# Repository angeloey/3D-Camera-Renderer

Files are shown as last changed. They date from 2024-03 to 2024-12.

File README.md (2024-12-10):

//Angelo Maoudis README // 14074479 

# An Infrared 3D Camera & Graphics Renderer
Built from scratch as part of my Embedded Systems Programming Module

An embedded system to scan an object, then render the resulting scan in 3D to be inspected & interacted with by the user.

## 1 - Embedded System Proposal

Description: A 3D Scanner.
A device which scans a scene along the X and Y axis, while recording Z axis data about the scene. A 2D representation of the scene, alongside a 3D render is generated from the recoded data, which the user can interact with to inspect the object/scene post scan. Colour is used to represent depth in the 2d Image.

Basic operation:
The device uses a stepper motor and a servo to take range measurements in increments of 1 degrees, in a 90x90 degree FOV.\
The range measurements are made using an IR Sensor, the maximum range of which can be configured using an potentiometer.\
During and after completion of the scan, the data recorded is used to represent the scanned scene on the LCD Screen. The user can interact with a 3D render of the scanned scene via the touchscreen, or by selecting an option to automatically rotate the render via the rotary encoder menu.\
Uart Commands can also be used to start a scan remotely.

The system also contains customization options such a colour slider, and fov adjustment, which are modified in their corresponding menu via the touchscreen interface.

Verification of Successful Operation:
The fundamental operation of the system can be considered successful if a scene/object can be scanned by the device, producing a render which can be interacted with by user. I.e. can be rotate around all 3 Axis at will. A wide array of diferent technologies and peripherals will be used by the system to achieve this, and will work together without error or conflict.

## 2 - Hardware Design

Component List:

STM32f74NG-DISCO

Inputs:
 - Uart via Serial Port - STM32F74NG-DISCO
 - Potentiometer - NHP22
 - Rotary Encoder - EC11
 - IR Range Sensor - GP2Y0A21YK
 - Touchscreen - STM32F74NG-DISCO

Outputs:
 - Uart via Serial Port - STM32F74NG-DISCO
 - LCD Screen - STM32F74NG-DISCO
 - Servo Motor - SG90
 - Stepper Motor - PJJ051ZA-P

STM32F74NG-DISCO Datasheet: https://www.farnell.com/datasheets/1944312.pdf \
IR Sensor Datasheet: https://www.sparkfun.com/datasheets/Components/GP2Y0A21YK.pdf \
Potentiometer Datasheet: https://p3america.com/content/pdf/nhp22.pdf \
Rotary Encoder Datasheet: https://www.farnell.com/datasheets/1837001.pdf \
Servo Datsheet: https://static.rapidonline.com/pdf/37-1330t.pdf \
Stepper Motor Datsheet: University Provided, cannot find information online, generic unipolar stepper operation. \
ULN2803 Darlington Array Datasheet: https://www.st.com/resource/en/datasheet/uln2801a.pdf

Connection Diagram: \
connection diagram

System Runs on MbedOS 6 \
MbedOS Docs: https://os.mbed.com/docs/mbed-os/v6.16/introduction/index.html 

To stay within the "spirit" of the Embedded Systems Programming module, the System opts for software control over hardware control, via the GPIO, ADC, & DAC pins built in to the STM32f746NG-DISCO, with the only exception being the use of a ULN2803 Darlington Array IC which is used as a *driver* for the stepper motor. Stepper motor *control* is achieved via software implementation however.

## 3 - Embedded Code Implementation and Architechture

### Structure Overview

The system uses a combination of hard and soft interrupts, polling, and multithreading. \
This was an intentional design choice in order to demonstrate/implement a wider range of techniques. \
Hardware interrupts are used to control the physical IO of the device, such as the rotary encoder & menu navigation. \
Software interrupts (Tickers) are used to progress through the scanning process, as well as to refresh the LCD display. \
The touchscreen interface is handled by its own dedicated thread, running in paralell to the main thread of the device. Semaphores are used to manage the individual threads, and to ensure a thread only uses system resources when necessary. \
A polling scheme is used to manage the UART interface.  \
A flag polling system is also used to manage routines triggered by interrupts without executing them inside the ISR, both to avoid unwanted mutex locks, 
and to adhere to best practices (i.e. no delays or lengthy functions inside the ISR). 

Functionality of peripheral devices is contained and managed by individual Objects & corresponding libraries. 

All source files are commented where apporopriate to provide a reasonable level of documentation, "Pseudo Diagrams" have been drawn using comments in files where a greater level of explanation was felt necessary, example below from My-Stepper-Lib:

pseudodiagrams

### Tasks Handled by Software

### Scene/Object Scanning:
__Description__: The scanning routine is responsible for triggering & reading peripheral devices such as the stepper motor, servo, IR sensor,
and potentiometer. And displaying the progress of the scan to the user.
        
__Real-time Constraints__: During scanning data is collected from these peipherals, and output output to the motors in realtime as the scan progresses.
A 2D representation of the scene, as well as a 3D render of the scanned object is updated in realtime to indicate scan progress to the user.
        
__Responsiveness__: The system only allocates resources to areas required by this routine as and when they are needed. These resources are managed by a series of flags set and unset by the Scanning routine as the scan progresses.

### Hardware Interface Interaction:
__Description__: A rotary encoder is used to cycle through a menu, which provides primary method of user interaction with the system.
        
__Real-time Constraints__: This is handled using hardware interrupts, and will take priority over all tasks so that the user can control the device               without hinderence, with the exception of the scanning routine. If the scanning routine is currently running, the vertices from the last successfull scan are loaded into the vertex buffer before executing any instructions, to avoid any unfinished scans being loaded by the renderer.
        
__Responsiveness__: As mentioned above, this is handled by hardware interrupts to provide immediate response to user interaction.

### Touch Interface:
__Description__: Detecting touch on the LCD in specific areas, and executing tasks accordingly. The touch interface consists of 9 touch buttons used to rotate a scanned object in 3D, as well as to alter the camera focal length of the renderer. Additionally a slider is also used to change the draw colour of the system.
        
__Real-time Constraints__: Handled by its own dedicated thread that runs alongside the main thread of the system in order to respond to user interaction in realtime. \ This was intentional in order to demonstrate a wider range of technologies. Semaphores are used to ensure that the touch interface thread only consumes system resources when touchscreen buttons are visible on the screen.
        
__Responsiveness__: Since it is handled by its own thread, responsiveness to touch inputs is immediate, and has support for multiple simultaneous touches

### Uart Interface:
__Description__: A barebones uart interface is used to trigger the scanning routine remotely, upon recieveing a newline (\n) character via the serial port, the device compares the characters stored in its character buffer to a list of known commands, and executes hte corresponding command accordingly. If none are found, it notfies the user that it does not recognise the recived command. This was included primarily to better satisfy the marking criteria and demonstrate the use of serial communication, but finds itself analagous to existing embedded systems where remote activation is a desired feature.

__Real-time Constraints__: Characters are added to a buffer as and when they are recieved by the device, not particularly time-critical and is polled once any set flags have been acknowledged.

__Responsiveness__: No noticeable delay by the user. Effectively immediate from a humans POV.

### 3D Rendering:
__Description__: The device is capable of representing the data recorded by the scanning routine in the form of a weak perspective projection. The files inside folder My-3D-Lib are heavily commented to explain how the 3D rendering of the system is achieved, below is an attempt to illustrate how the "Projected" pixel coordinates are calculated from the vertices recorded by the Scanning routine, for the X axis. This process is repeated for each coordinate recorded (90 x 90 = 8100).

3d_rendering

 Triangles (X, Adjacent, C) and (Xp, Focallength, C) are similar, \
 therefore: Xp / X  ==  FocalLength / Adjacent \ 
 thus Xp  ==  (Focallength * X) / Adjacent \
 Xp (xProjected) is the X coordinate of the pixel intersected when casting a ray from the camera to the object. \
 Repeat for Y. Process is analagous. \
 Repeating this process for all scanned coordinates results in a list of XY pixel coordinate which when drawn on the screen \
 form a weak perspective projection of the scanned Scene/Object. 

__Real-time Constraints__: During scanning, a 3D render of the scene is constructed in realtime as the system records more data. However this render does not need to rotate, and given that the scan operates at a frequency of 20Hz, and each pixel is calculated as its corresponding vertex is obtained in realtime, ample time is available to render the scene in realtime. \
Once the scan has completed, the object can be rendered, rotated, and inspected by the user. This involves significantly more computational overhead and the frame-rate of the system is limited by the speed at which the FPU can complete these calculations.

__Responsiveness__: When rotating and inspecting the render, the system becomes significantly less responsive, and "Double-Buffering", along with V-Sync was implemented in order to eliminate screen tearing/flickering, as the device cannot calculate and draw all of the projected vertices fast enough to be imperceptible without this.

### Source Code Authors
Files written by me: 
 - Everything in a folder labelled "My-X"
 - main.cpp
 - README.md
 - Unit tests inside folder TESTS (Made from boilerplate provided in mbed docs, link to boilerplate provided as comments inside each file).
 All files are labelled with Name and SID as top comments.

Third-Party Code: 
 - BSP_DISCO_F746NG.lib
 - Mbed-OS.lib

### Practical Embedded Considerations

The scan system was originally made using an ultrasonic sensor, and a library for this sensor sourced from mbed.org, however the output was noisy and I intend to write all libraries for components myself. To solve this issue replaced with IR range sensor (much less noisy output) and wrote library from scratch (My-IR-Lib).

In order to target the IR Range sensor at a specific point, a Mount was designed and 3D-Printed, the latest version of this model in STL format is included in the repository under folder: 3D Print Files

The image below shows from left to right, Versions 1, 2, 3, & 4, of the aforementioned mount:

3d_mounts

Rotating a perspective projection render in 3 dimensions is computationally expensive, and somewhat out of reach for a device such as the STM32F7 to do in any reasonable amount of time. However this system takes advantage of a "workaround". 
Provided you only rotate around one axis at a time, a perspective projection can be rotated using the 2D rotation matrix, which is much less computationally expensive.
To provide rotation around all 3 axis, this system rotates around one axis, saves the result to a buffer, and then rotates the resulting buffer around another axis sequentially. this workaround means that the system can appear to rotate a render around 3 axis simultaneously, albeit while taking 3 times as long to do so.

Functionality was written into the stepper library to enable microstepping, however the STM32f7 Board being used for this system only has 2 onboard ADC's and the implementation (the only way i could think of to do it in software) required 4 ADC's to operate. 
As the step size of the provided stepper motor is too large for the degree of accuracy desired, the system only rotates the stepper every 4 degrees instead of every 1 degree, and takes 4 measurements during its travel time to acquire the closest approximation I could get. 
I am unable to find any information on this specific stepper online, but measuring its step size by hand, it appears to have a step size of ~7.5 Degrees, so I am using half stepping to get this down to ~4, and using the aforementioned method to compensate for it.

## 4 - Evaluation 
### Implementation Successfulness
The system achieves the criteria outlined in the proposal, it is capable of scanning scenes or objects and generating a 3D render which the user can freely rotate along all three axis. It utilises a wide range of technologies and peripherals, which operate without conflict. 
The system can be considered a sucessful prototype.

Upon reflection, some shortcomings of the device or things I would add given more time include:
- Ability to export renders to another device (maybe as .STL or similar).
- The stepper motor used for the project works fine as a proof of concept/prototype however in a future iteration i would substitute it for a stepper with a smaller minimum step angle, or use a MCU with multiple DAC's as to utilize microstepping
- Create an enclosure or housing for the device (Maybe a battery powered handheld iteration)
- Create a PCB implementation instead of relying on a breadboard
- Add greater functionality to the uart interface. a HC-05 module could be used along side a terminal app, to control the device from a phone

### Group Members:
Angelo Maoudis 14074479 \
Commits as: maoudisa(University Github) & angeloey (Home Github). 

## Link to Video Demonstration:
https://youtu.be/fXoxNYmKON4

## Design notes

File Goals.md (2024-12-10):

### Goals & Pre-Project Discussion:
Goals for the Assignment. \
Namely, the objectives defined in the marking criteria, and how i intend to achieve each one.

#### Grade:
100%.
Satisfy all marking criteria to a maximum

#### Complexity (Technologies):
the goal of the project will be to develop the aforementioned embedded system using a range of technologies as to satisfy the assignment criteria.\
The system will purposely include a range of technologies, even in scenarios where it would traditionally make sense to use multiple instances of a
single technology, for example: instead of using two stepper motors (one for x movement and one for y movement), this project will make use of a
stepper motor for x movement and a servo motor for y movement.\
or by using a rotary encoder and a potentiometer, where two potentiometers would suffice.\
While this may not be the most practical approach, it affords me the opportunity to write a library for, and implement the use of more technologies which will better aid the achievement of the following excerpt from the marking criteria:

*"a wide range of complex\
input and output devices some of\
which we may not have used in\
the tutorial material, all working\
as expected."*

#### Version Control (Regular Commits and a Clear Workflow):
Another goal of the project is to provide a meaningful and well commented/documented update to the repository at regular intervals. \
(I will aim for daily commits, however: life waits for no man.) \
Any periods without a commit will be compensated for in magnitude or quantity once updates resume. \
There are 27 days between the start of this project on March 6th, and the due date April 2nd, therefore I will ensure there are at MINIMUM, 27 commits of
substanstial size, quality, or progress before April 2nd. \
Each commit will aim to demonstrate a clear direction and progress route through the projects development, i.e. evidence i havent just copied a load of
stuff i dont understand from stackoverflow.

I consider a meaningful update to be along the lines of, but not limited to, the following :

 - Functional progress in, or the completion of, a library for a component (.h and .cpp files in folder designated: "My-X-Lib"). 
 - Well commented, significant progress on the functionality of the project. 
 - Significant progress in, or beginning of, the Implementation of a new technology (a functional addition to debug screen for example.).
 - "Housekeeping": formatting, commenting, & encapsulating code to better reflect OOP practices etc.
 - Checkoints, functional milestones, or working implementation of a feature, such as a demo (i.e. "50Hz Rotating Cube Demo" on March 18th).

TL;DR:
Regular updates of some significance, with an accurate commit message.\
No "added some code" commits.\
Clear workflow and direction should be visibile throughout commit history (once target embedded system has been decided).\

this is with the intention of achieving the following assignment criteria excerpt:

*"Evidence of regular daily\
commits over a longer time\
frame. Demonstrates clear\
incremental progress with logical\
commit messages for features etc."*

#### Code Quality:
Write practical code and follow best practices throughout all aspects of the assignment, including but not limited to things such as:

 - dont use delays in an interrupt, dont use GOTO: etc.
 - dont name variables things like: "foo", "bar", and "var1", code should be "self documenting" and readable.
 - use MEANINGFUL comments as a form as documentation, no functions without comments, but also dont have a useless comment on every single line.
 - need to call the same bit of code many many times? PUT IT IN A FUNCTION/CLASS/LIBRARY.
 - camelCase is king.
 - dont use uint32_t where uint8_t would suffice. not exclusive to integers. *(Exception: Chris said it's ok to "throw floats at it")*

(I will consider myself exempt from these restrictions during development/debugging, however final code should follow all without exception). \
the following assignment criteria is self explanitory, I will attempt to be a good code monkey:

*Outstanding tidy code. Good\
practices being used e.g.\
encapsulation, meaningful\
identifiers and an attempt at\
documentation. Code contains\
no linting errors or warnings."*

Additional overlap from the following excerpt:

*"Use of custom classes, objects,\
and OOP concepts."*

### Naming Convention adhered to:
- Variables: camelCase
- User-Defined/Custom Types: PascalCase
- Constants: CAPS_SEPARATED_BY_UNDERSCORES
- Private Member Variables: /_underscorePrefixedCamelCase
- Descriptive Self-Documenting identifiers are mandatory. 

#### Complexity & Architechture (Embedded Code)

the following criteria is self explanitory, dont have the entire thing in a while loop:

*"The embedded architecture used\
likely makes use of a\
combination of hard and soft\
interrupts with polling or perhaps,\
RTOS, multi-threading, event\
loops, etc."*

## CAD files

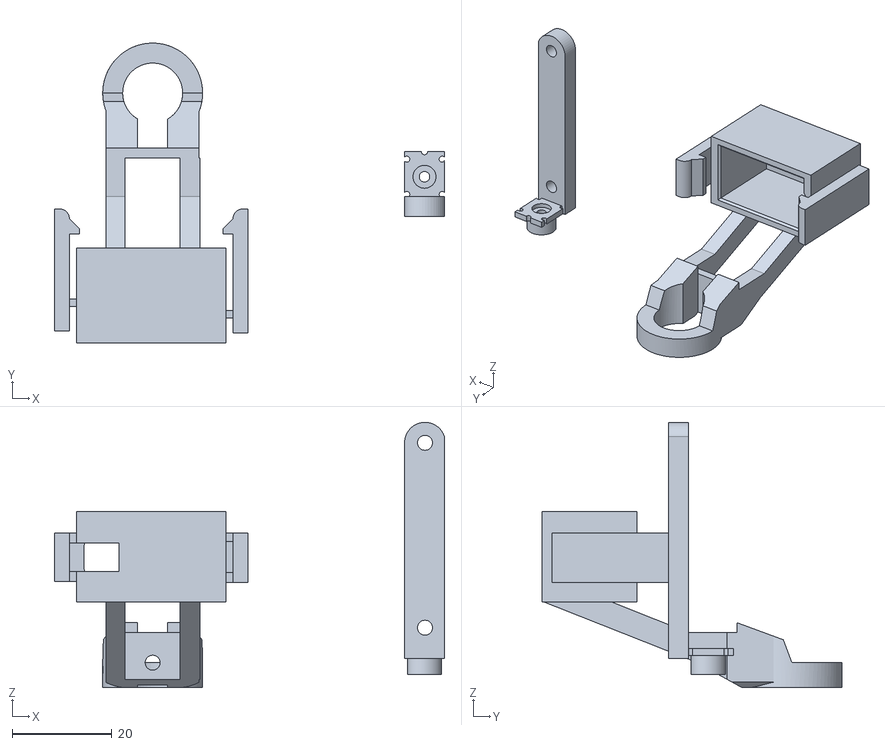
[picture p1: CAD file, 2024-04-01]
3D Print Files/Angelo_IR_Mount_V4.stl
78.1 x 60.0 x 53.1

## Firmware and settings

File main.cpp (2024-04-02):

// Angelo Maoudis 14074479
#include "mbed.h"
#include "rtos.h"
#include "stm32746g_discovery_lcd.h"
#include "stm32746g_discovery_ts.h"
#include "math.h"
// My Libs
#include "irSense.h"
#include "myUtils.h"
#include "pot.h"
#include "myServo.h"
#include "myStepper.h"
#include "rotaryEncoder.h"
#include "my3d.h"
#include "myButtons.h"
#include "uartCommands.h"

    // Magic Numbers / Constants                 // Using constexpr over #define for evaluation at compile time. Considered better practice in modern c++
namespace constants{
        // Menu/Option Constants
    constexpr int8_t MAX_MENU_ENTRIES = 4 -1;
        // Offsets/Coordinates for drawing on LCD
    constexpr uint8_t OFFSET_3D_X = 240;         // Offsets for drawing 3D object centred on (0,0) which is at the top left of the LCD.
    constexpr uint8_t OFFSET_3D_Y = 127;
    constexpr uint8_t OFFSET_RADAR_X = 110;      // Position offsets for drawing radar view.
    constexpr uint8_t OFFSET_RADAR_Y = 202;
    constexpr uint16_t OFFSET_DEPTHMAP_X = 310;  // Position offsets for drawing depth map.
    constexpr uint8_t OFFSET_DEPTHMAP_Y = 202;
}

    // Function declarations
void incrementScan(void);
void drawRadarView(float distance, float angle);
void drawDepthMap(float irDistance, float scanAngle, uint8_t scanLayer, uint8_t maxRange);
void updatePeripherals(float currentIrDistance, float currentScanAngle, uint8_t currentScanLayer, float currentPotReading);
void rotaryButtonPressed(void);
void rotaryTurned(void);
void draw3dObject(void);
void rotatingCubeDemo(void);
void drawDebugCube(void);
void manualRotation(void);
void tsButtonThreadFunction(void);
void toggleLCDLayer(void);
void startScanUart(void);

    // Obtaining XYZ values via scan
bool scanningClockwise = false; // Scan direction: False = CCW(-X), True = CW(+X) 
int8_t desiredScanAngle = 0;   // Scan/Stepper angle (Horizontal/X Axis)
uint8_t depthMapLayer = 0;      // Y value/layer of depthmap, also used for Servo angle (Vertical/Y Axis)
uint8_t rangeCutoff = 100;      // Any distances sensed past this value, are capped to this value (Depth/Z Axis)

    // Flags, mostly for executing functions incompatible with ISR (mutex, too slow, etc.)
bool progressScanFlag = false;  // Scan object flag, progress through 3D scan when this flag is set.
bool draw3dObjectFlag = false;  // Draw 3D object when this flag is set.
bool spinRenderFlag = false;    // Rotate 3D object automatically when this flag is set.
bool rotateTouchFlag = false;   // Enable touch buttons flag.
bool loadTestCubeFlag = true;   // Until this flag is un-set, 3D renderer draws a tri-coloured cube.
bool drawDebugFlag = false;     // Draw Debug-Screen. Peripheral data, etc.

    // Menu navigation/control
int8_t menuCounter = 0;         // Used to store last/select a menu option via rotary Encoder.
uint8_t rotationAxis = 0;       // Axis of rotation for 3D objects. 0, 1, 2 == X, Y, Z.
uint16_t pixelIndex = 0;     // Current xyz index to write/read.

    // Misc.
uint32_t drawColour = LCD_COLOR_YELLOW; // This is modified by SliderDrawColour. Default setting is yellow.
uint8_t redArgb = 0xFF;                            
uint8_t greenArgb = 0xFF;                // ARGB values, used to cycle through ARGB spectrum via slider. Alpha is always 0xFF when these are used
uint8_t blueArgb = 0xFF;                 // Default is 0xFF (255) (white)
uint16_t lastX;                          // Coordinates of last drawn line for radar view, used to overwrite in black without clearing entire radar.
uint16_t lastY;                          // purely cosmetic.
int activeLCDLayer = 0;

    // Initialization, Peripheral Objects/Structs.
IrSense IR(A0);                                     // initialize IR sensor, reading from Pin A0
Pot RangePot(A1);                                   // initialize Potentiometer, reading from Pin A1
Servo Servo(D0, 90, 2, 1.5);                     // initialize Servo motor, on pin D0, with a 180 degree range between 1.5 and 2ms.
Stepper Stepper(D1, D2, D3, D4, 7.5);               // initialize Stepper motor, on pins D1, D2, D3, D4, with a step angle of 7.5
Rotary Encoder(D5, D6, D7, &rotaryButtonPressed, &rotaryTurned);    // initialize Rotary Encoder on D5,D6,D7, and pass functions to object
//MicroStepper Stepper(A5, A4, A3, A2, 7.5);        // Cant use microstepping as the board only has 2 DAC outs :(
Object3D Render3D(-200);  // initialize 3D Object
TS_StateTypeDef Touchstate;                         // Touchscreen-state Struct
UartInterface UartSerial(USBTX, USBRX, 115200, &startScanUart);

    // Initialization, Touchscreen Button Objects
Button ButtonIncreaseRotationX(420, 460, 52, 92, LCD_COLOR_RED, LCD_COLOR_YELLOW, 1, Touchstate);               // Rotate around z axis
Button ButtonDecreaseRotationX(420, 460, 180, 220, LCD_COLOR_RED, LCD_COLOR_YELLOW, 2, Touchstate);
Button ButtonDecreaseRotationY(140, 180, 225, 265, LCD_COLOR_GREEN, LCD_COLOR_YELLOW, 3, Touchstate);           // Rotate around y axis.
Button ButtonIncreaseRotationY(300, 340, 225, 265, LCD_COLOR_GREEN, LCD_COLOR_YELLOW, 4, Touchstate);
Button ButtonIncreaseRotationZ(20, 60, 52, 92, LCD_COLOR_BLUE, LCD_COLOR_YELLOW, 5, Touchstate);                // Rotate around z axis.
Button ButtonDecreaseRotationZ(20, 60, 180, 220, LCD_COLOR_BLUE, LCD_COLOR_YELLOW, 6, Touchstate);
Button ButtonResetRotation(350, 470, 230, 262, LCD_COLOR_MAGENTA, LCD_COLOR_CYAN, 0, Touchstate);               // Restore to saved vertices.
Button ButtonDecreaseFov(75, 130, 230, 262, LCD_COLOR_DARKCYAN, LCD_COLOR_WHITE, 0, Touchstate);                // fov-, Increases focal length.
Button ButtonIncreaseFov(10, 65, 230, 262, LCD_COLOR_DARKBLUE, LCD_COLOR_WHITE, 0, Touchstate);                 // fov+, Decreases focal length.
Slider SliderDrawColour(10, 65, 10, 42, LCD_COLOR_LIGHTMAGENTA, LCD_COLOR_WHITE, 0, Touchstate, true, 30, 450); // Change drawing colour via slider

    // Classes/Mbed Objects, Tickers/Interrupts/Etc.
Utilities Utils;            // Utilities class. Frequently used, non program-specific functions.
Ticker TickerNextStep;      // used to iterate through object scan
Ticker TickerUpdateScreen;  // Refresh screen with updated view from selected mode, normally 50Hz

    //Threads / RTOS / Mutex
Thread ThreadTSButtons;       // Dedicated thread for handling TS Button Presses
Mutex MutexTSButtons;         // Mutex lock for when reset button needs to load (8100*3) vertices.
Semaphore SemaphoreTSButtons(1, 1); // Semaphore, used to control execution of TS Button thread

//----------------------------Function definitons--------------------------------------------
    // Used to start scan via uart
void startScanUart(void){
    BSP_LCD_Clear(LCD_COLOR_BLACK);
    TickerUpdateScreen.detach();
    TickerNextStep.detach();
        // Attatch ticker to this flag. Increments scan progress
    TickerNextStep.attach(incrementScan, 20ms); // 50Hz
}

    // Select & Execute menu options when button is pressed // Triggered by interrupts in rotary lib
void rotaryButtonPressed(void){
    for(int i = 0; i < 2; i++){
        BSP_LCD_Clear(LCD_COLOR_BLACK);
        switch(menuCounter){
        case 0:
            TickerUpdateScreen.detach();
            TickerNextStep.detach();
                // Attatch ticker to this flag. Increments scan progress
            TickerNextStep.attach(incrementScan, 20ms); // 50Hz
            break;
        case 1:
            TickerUpdateScreen.detach();
            TickerNextStep.detach();
                // Attatch ticker to this flag. Redraws Object
            TickerUpdateScreen.attach(draw3dObject, 20ms); // 50Hz
            spinRenderFlag = true;
            break;
        case 2:
            TickerUpdateScreen.detach();
            TickerNextStep.detach();
                // Restore 3D object from save
            Render3D.restoreSave();
                // Draw buttons
            BSP_LCD_SetTextColor(LCD_COLOR_ORANGE);
            BSP_LCD_DrawRect(79, 49, 321, 156);
            ButtonIncreaseRotationX.drawButton(); ButtonDecreaseRotationX.drawButton();
            ButtonIncreaseRotationY.drawButton(); ButtonDecreaseRotationY.drawButton();
            ButtonIncreaseRotationZ.drawButton(); ButtonDecreaseRotationZ.drawButton();
            ButtonIncreaseFov.drawButton(); ButtonDecreaseFov.drawButton();
            ButtonResetRotation.drawButton();
            SliderDrawColour.drawButton();
            BSP_LCD_SetFont(&Font16);
            BSP_LCD_SetTextColor(LCD_COLOR_YELLOW);
            BSP_LCD_DisplayStringAt(80, 241, (uint8_t*)"fov-", LEFT_MODE);
            BSP_LCD_DisplayStringAt(15, 241, (uint8_t*)"fov+", LEFT_MODE);
            BSP_LCD_DisplayStringAt(365, 241, (uint8_t*)"reset", LEFT_MODE);
            BSP_LCD_SetFont(&Font12);
                // Attatch ticker to this flag. Rotates and draws based on ts input
            TickerUpdateScreen.attach(manualRotation, 1ms); // 50Hz
            break;
        case 3:
            drawDebugFlag = !drawDebugFlag;
            break;
        default:    // should never happen
            BSP_LCD_DisplayStringAt(0, LINE(1), (uint8_t *)"Something went wrong (rotaryButtonPressed)", CENTER_MODE);
            break;
        }
    }
}

    // Scroll through menu when Encoder is turned
void rotaryTurned(void){
    (Encoder.getClockwise() == true) ? menuCounter++ : menuCounter--;
    if(menuCounter > constants::MAX_MENU_ENTRIES){
        menuCounter = 0; 
    }else if(menuCounter < 0){
        menuCounter = constants::MAX_MENU_ENTRIES;
    }
    BSP_LCD_ClearStringLine(1);
    BSP_LCD_SetTextColor(LCD_COLOR_YELLOW);
    switch(menuCounter){
        case 0:
            BSP_LCD_DisplayStringAt(0, LINE(1), (uint8_t *)"Menu: Start Scan", CENTER_MODE);
            toggleLCDLayer();
            BSP_LCD_DisplayStringAt(0, LINE(1), (uint8_t *)"Menu: Start Scan", CENTER_MODE);
            break;
        case 1:
            BSP_LCD_DisplayStringAt(0, LINE(1), (uint8_t *)"Menu: Rotate Scanned Object", CENTER_MODE);
            toggleLCDLayer();
            BSP_LCD_DisplayStringAt(0, LINE(1), (uint8_t *)"Menu: Rotate Scanned Object", CENTER_MODE);
            break;
        case 2:
            BSP_LCD_DisplayStringAt(0, LINE(1), (uint8_t *)"Menu: Manual Object Rotation", CENTER_MODE);
            toggleLCDLayer();
            BSP_LCD_DisplayStringAt(0, LINE(1), (uint8_t *)"Menu: Manual Object Rotation", CENTER_MODE);
            break;
        case 3:
            BSP_LCD_DisplayStringAt(0, LINE(1), (uint8_t *)"Menu: Debug Mode", CENTER_MODE);
            toggleLCDLayer();
            BSP_LCD_DisplayStringAt(0, LINE(1), (uint8_t *)"Menu: Debug Mode", CENTER_MODE);
            break;
        default:    // should never happen
            BSP_LCD_DisplayStringAt(0, LINE(1), (uint8_t *)"Something went wrong (rotaryTurned)", CENTER_MODE);
            break;
    }
}

    // Draw radar representaion of current scan (X&Z progress along each Y layer)
void drawRadarView(float irDistance, float scanAngle){ 
    BSP_LCD_SetTextColor(LCD_COLOR_BLACK);
    BSP_LCD_DrawLine(constants::OFFSET_RADAR_X, constants::OFFSET_RADAR_Y, lastX + constants::OFFSET_RADAR_X, lastY + constants::OFFSET_RADAR_Y); // overwrite last drawn line in black
    uint16_t x = irDistance * cos(constants::PI_DOUBLE * 2 * (scanAngle + 225) / 360); 
    uint16_t y = irDistance * sin(constants::PI_DOUBLE * 2 * (scanAngle + 225) / 360); // find x,y coords of a point on a circle, of radius 'distance' at angle 'angle'
    BSP_LCD_SetTextColor(LCD_COLOR_WHITE);
    BSP_LCD_DrawLine(constants::OFFSET_RADAR_X, constants::OFFSET_RADAR_Y, x + constants::OFFSET_RADAR_X, y + constants::OFFSET_RADAR_Y); // draw a line from radar offset, to x,y + offset
    BSP_LCD_SetTextColor(LCD_COLOR_YELLOW);
    BSP_LCD_DrawCircle(x + constants::OFFSET_RADAR_X, y + constants::OFFSET_RADAR_Y, 1); // mark the end of the line with a yellow blob
    BSP_LCD_DrawLine(x + constants::OFFSET_RADAR_X, y + constants::OFFSET_RADAR_Y, lastX + constants::OFFSET_RADAR_X, lastY + constants::OFFSET_RADAR_Y); // connect the blobs
    lastX = x; // store last used x,y values
    lastY = y;
}

    // Draw 2D image with depth data. Closer distance = brighter pixel
void drawDepthMap(float irDistance, float scanAngle, uint8_t scanLayer, uint8_t maxRange){ 
    uint16_t drawX = (scanAngle) + constants::OFFSET_DEPTHMAP_X; //0-90deg from left = x coord 0 to 90 from offset //TODO: "normalise" the image so it isnt skewed 
    uint16_t drawY = constants::OFFSET_DEPTHMAP_Y - scanLayer;                                                     //(Z = cos(angle) * distance??? check maths before implementing)
    uint8_t redBrightness = Utils.valMap(irDistance, 0, maxRange, 0xFF, 0x00);
    BSP_LCD_DrawPixel(drawX, drawY, Utils.argbToHex(0xFF, redBrightness, 0x00, 0x00));
        // Draw bounding box
    BSP_LCD_SetTextColor(drawColour);
    BSP_LCD_DrawRect(constants::OFFSET_DEPTHMAP_X - 1, constants::OFFSET_DEPTHMAP_Y - 91, 91, 91);
}
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
int main(){
    
        // Setup LCD, Show startup message, Clear to black
    BSP_LCD_Init();
    BSP_LCD_SetXSize(480); BSP_LCD_SetYSize(272);
    BSP_LCD_LayerDefaultInit(LTDC_ACTIVE_LAYER, LCD_FB_START_ADDRESS);
    BSP_LCD_SelectLayer(LTDC_ACTIVE_LAYER);
    BSP_LCD_DisplayStringAt(0, LINE(5), (uint8_t *)"14074479 MAOUDISA", CENTER_MODE);
    HAL_Delay(1000);
    BSP_LCD_SetFont(&Font12);
    BSP_LCD_SetBackColor(LCD_COLOR_TRANSPARENT);
    BSP_LCD_SetTextColor(LCD_COLOR_WHITE);
    BSP_LCD_Clear(LCD_COLOR_BLACK);

        // Setup another LCD layer
    BSP_LCD_LayerDefaultInit(0, LCD_FB_START_ADDRESS +(272*480*4));
    BSP_LCD_SelectLayer(0);
    BSP_LCD_DisplayStringAt(0, LINE(5), (uint8_t *)"14074479 MAOUDISA", CENTER_MODE);
    HAL_Delay(1000);
    BSP_LCD_SetFont(&Font12);
    BSP_LCD_SetBackColor(LCD_COLOR_TRANSPARENT);
    BSP_LCD_SetTextColor(LCD_COLOR_WHITE);
    BSP_LCD_Clear(LCD_COLOR_BLACK);

        // Initialize touchscreen
    BSP_TS_Init(480, 272);

        // Attatch ticker to this flag. Using this demo as a splash screen
    BSP_LCD_SelectLayer(0); BSP_LCD_SetLayerVisible(0, ENABLE); BSP_LCD_SetLayerVisible(1, DISABLE);
    TickerUpdateScreen.attach(rotatingCubeDemo, 1ms); 

    // Do nothing here until a flag is set
    while(1) {

             // Wait for v-sync before drawing next frame. (Magic.)
        while (!(LTDC->CDSR & LTDC_CDSR_VSYNCS)) {}

            // Manual control over 3D render (Slow)
        if(rotateTouchFlag == true){
            toggleLCDLayer();
                // Relinquish control of Semaphore so TSButton thread can run
            SemaphoreTSButtons.release();
                // Attatch thread to monitor TS Buttons and rotate render accordingly, does nothing once thread is started.
            ThreadTSButtons.start(tsButtonThreadFunction);
                // Generate coordinates, Clear Object, Draw image. (Only clear immidiately before drawing to reduce strobing)
                // Buttons are not redrawn, But also not cleared. Faster. (Exception -> Sliders)
            Render3D.generateProjected();
            //SCB_CleanDCache();
            if(loadTestCubeFlag == true){
                drawDebugCube();
            }else{
                BSP_LCD_SetTextColor(LCD_COLOR_BLACK);
                BSP_LCD_FillRect(80, 50, 320, 155);
                BSP_LCD_SetTextColor(drawColour);
                for(int i = 0; i < constants::MAX_VERTICES -1; i++){
                    BSP_LCD_DrawLine(Render3D.xProjected[i] +constants::OFFSET_3D_X, Render3D.yProjected[i] +constants::OFFSET_3D_Y, Render3D.xProjected[i+1] +constants::OFFSET_3D_X, Render3D.yProjected[i+1] +constants::OFFSET_3D_Y);
                }
            }
        }

            // Scanning Routine, progress one step (causes mutex if in ISR)
        if(progressScanFlag == true){
            BSP_LCD_SelectLayer(1); BSP_LCD_SetLayerVisible(1, ENABLE); BSP_LCD_SetLayerVisible(0, DISABLE);
                // Take semaphore so TSButtons cant run
            SemaphoreTSButtons.try_acquire();
                // Update peripheral data. Clear LCD between layers
            updatePeripherals(IR.getDistance(), desiredScanAngle, depthMapLayer, RangePot.readVoltage());
            (scanningClockwise == true) ? desiredScanAngle++ : desiredScanAngle--;
            if(desiredScanAngle >= 90 || desiredScanAngle < 0){
                scanningClockwise = !scanningClockwise;
                lastX = 0, lastY = 0;
                depthMapLayer++;
                depthMapLayer++;
                BSP_LCD_SetTextColor(LCD_COLOR_BLACK);
                BSP_LCD_FillRect(0, 22, 300, 250);
                    // Check for scan completion. Detatch ticker & save Vertices
                if(depthMapLayer > 90){
                    TickerNextStep.detach();
                    depthMapLayer = 0;
                    pixelIndex = 0;
                    Render3D.saveVertices();
                    draw3dObjectFlag = true;
                }
            }
                // Move Stepper and Servo. Store xyz Coordinates
            if(desiredScanAngle %4 == 0) {Stepper.step(scanningClockwise, 1, 7);} // Uni only has crap Steppers. (step angle too large, even with half step)
            Servo.writePos(depthMapLayer);
            Render3D.Vertices.y[pixelIndex] = -45 + depthMapLayer;
            Render3D.Vertices.x[pixelIndex] = -45 + desiredScanAngle;
            Render3D.Vertices.z[pixelIndex] = (int16_t)(rangeCutoff / 2) - round(IR.lastDistance());
            if(IR.lastDistance() >= rangeCutoff) {Render3D.Vertices.z[pixelIndex] = -(int16_t)(rangeCutoff / 2);}
            pixelIndex++;
            draw3dObjectFlag = true; // Draws 3d object as it is scanned
            progressScanFlag = false;
        }

            // Draw scene/object in 3D (Dont want this in ISR, lots of operations).
        if(draw3dObjectFlag == true){
            BSP_LCD_SelectLayer(1); BSP_LCD_SetLayerVisible(1, ENABLE); BSP_LCD_SetLayerVisible(0, DISABLE);
                // Take semaphore so TSButtons cant run
            SemaphoreTSButtons.try_acquire();
            if(spinRenderFlag == true){
                for(int j = 0; j < 360; j++){
                    Render3D.rotateVertices(j, rotationAxis);
                    Render3D.generateProjected();
                    BSP_LCD_SetTextColor(LCD_COLOR_BLACK);
                    BSP_LCD_FillRect(80, 50, 320, 155);
                    BSP_LCD_SetTextColor(drawColour);
                    for(int i = 0; i < constants::MAX_VERTICES -1; i++){ // Connect each projected vertex to its neighbour
                        BSP_LCD_DrawLine(Render3D.xProjected[i] +constants::OFFSET_3D_X, Render3D.yProjected[i] +constants::OFFSET_3D_Y, Render3D.xProjected[i+1] +constants::OFFSET_3D_X, Render3D.yProjected[i+1] +constants::OFFSET_3D_Y);
                    }
                        // Restore vertex data from save
                    Render3D.restoreSave();
                }
                rotationAxis++; // Cycle axis of rotation every full rotation
                if(rotationAxis > 2){
                    rotationAxis = 0;
                    TickerUpdateScreen.detach();
                }
            }else{
                Render3D.generateProjected();
                BSP_LCD_SetTextColor(drawColour);
                for(int i = 0; i < constants::MAX_VERTICES -1; i++){ // Connect each projected vertex to its neighbour
                    BSP_LCD_DrawLine(Render3D.xProjected[i] +constants::OFFSET_3D_X, Render3D.yProjected[i] +constants::OFFSET_3D_Y, Render3D.xProjected[i+1] +constants::OFFSET_3D_X,Render3D.yProjected[i+1] +constants::OFFSET_3D_Y);
                }
            }
            draw3dObjectFlag = false;
        }

            // Draw debug information on top of current screen. Toggleable.
        if(drawDebugFlag == true){
            while (!(LTDC->CDSR & LTDC_CDSR_VSYNCS)) {}     // Wait for v-sync before drawing next frame. (Magic.)
            BSP_LCD_SetTextColor(LCD_COLOR_YELLOW);
            char text [50];
            sprintf((char*)text, "IR Distance: %.2f    Voltage: %.2f", IR.getDistance(), IR.readVoltage()); 
            BSP_LCD_DisplayStringAt(0, LINE(2), (uint8_t *)&text, LEFT_MODE);
            float potVal = RangePot.readVoltage();
            sprintf((char*)text, "Range-Pot Distance: %d    Voltage: %.2f", Utils.valMap(potVal, 0, 3.3, 0, 100), potVal); 
            BSP_LCD_DisplayStringAt(0, LINE(3), (uint8_t *)&text, LEFT_MODE);
            sprintf((char*)text, "Encoder Clockwise: %d", Encoder.getClockwise()); 
            BSP_LCD_DisplayStringAt(0, LINE(4), (uint8_t *)&text, LEFT_MODE);
            sprintf((char*)text, "Servo Position: %.2f", Servo.readPos());
            BSP_LCD_DisplayStringAt(0, LINE(5), (uint8_t *)&text, LEFT_MODE);
            sprintf((char*)text, "Scan Clockwise: %d    Angle: %d   Layer: %d", scanningClockwise, desiredScanAngle, depthMapLayer);
            BSP_LCD_DisplayStringAt(0, LINE(6), (uint8_t *)&text, LEFT_MODE);
            sprintf((char*)text, "Radar Offset X: %d   Y: %d", constants::OFFSET_RADAR_X, constants::OFFSET_RADAR_Y); 
            BSP_LCD_DisplayStringAt(0, LINE(7), (uint8_t *)&text, LEFT_MODE);
            sprintf((char*)text, "DepthMap Offset X: %d   Y: %d", constants::OFFSET_DEPTHMAP_X, constants::OFFSET_DEPTHMAP_Y); 
            BSP_LCD_DisplayStringAt(0, LINE(8), (uint8_t *)&text, LEFT_MODE);
            sprintf((char*)text, "3D Array Index %d", pixelIndex); 
            BSP_LCD_DisplayStringAt(0, LINE(9), (uint8_t *)&text, LEFT_MODE);
        }
            // Process Uart input (if any)
        UartSerial.processInput();
    }
}

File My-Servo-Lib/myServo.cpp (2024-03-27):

// Angelo Maoudis 14074479
// Angelo myServo
#include "myServo.h"
#include <stdint.h>

Servo::Servo(PinName servoPin, uint16_t servoRange, float servoTimeStart, float servoTimeEnd):pwm(servoPin), _servoRange(servoRange), _servoTimeStart(servoTimeStart), _servoTimeEnd(servoTimeEnd){
    writePos(0);
    pwm.period_ms(20);
}

    // Have this here so that this library is not dependant on myUtils.h
    // Returns a mapped value of the input, from one numerical range to another.
float servoMap (float value, float istart, float istop, float ostart, float ostop){  
    float mappedVal = ostart + (ostop - ostart) * ((value - istart) / (istop - istart));
    return mappedVal;
}

    // Returns servo motors position in degrees
float Servo::readPos() {
    return _positionDegrees;
}

    // Sets new servo motor position. PWM output at pulsewidth corresponding to desired position.
    // Achieved by mapping the value "newPos" in range 0 -> _servoRange (degrees)
    // to its equivalent value in the range _servoTimeStart -> _servoTimeEnd (uSeconds).
void Servo::writePos(float newPos) {
    _positionDegrees = newPos;
    _position = servoMap(newPos, 0, _servoRange, (_servoTimeStart * 1000), (_servoTimeEnd * 1000));    // map: 0 -> _servoRange in degrees, to: _servoTimeStart -> _servoTimeEnd in uSeconds.
    pwm.pulsewidth_us(_position);
}

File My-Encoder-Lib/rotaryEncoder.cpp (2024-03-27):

// Angelo Maoudis 14074479
// Angelo rotaryEncoder
#include "rotaryEncoder.h"
#include "PinNamesTypes.h"
#include <cstdio>

Rotary::Rotary(PinName encoderA, PinName encoderB, PinName button, Callback<void(void)> buttonFunc, Callback<void(void)> turnFunc):_encoderA(encoderA),_encoderB(encoderB),_button(button),func(turnFunc){
    _clockwise = false;
    _encoderA.mode(PullDown);
    _encoderB.mode(PullDown);
    _button.mode(PullDown);

        // Call function passed here when button is pressed
    _button.rise(buttonFunc);

        // Update direction on rising edge Interrupts
    _encoderA.rise(callback(this, &Rotary::solveEncoder));
    _encoderA.fall(callback(this, &Rotary::solveEncoder));
}

    //  Read encoder states, and compare to previous states
    //  CW = A: 0 0 1 1     CCW = A: 0 0 1 1
    //       B: 1 0 0 1           B: 0 1 1 0
void Rotary::solveEncoder(void){
    uint8_t chanA = _encoderA.read(); // read channel A and B
    uint8_t chanB = _encoderB.read();
    _currentState = (chanA << 1) | (chanB); // storing states of A and B //2bit

    //11->00->11->00 is CCW
    //10->01->10->01 is CW
    if((_lastState == 0b11 && _currentState == 0b00)||(_lastState == 0b00 && _currentState == 0b11)){
        _clockwise = false;
        func();
    }else if((_lastState == 0b10 && _currentState == 0b01)||(_lastState == 0b01 && _currentState == 0b10)){
        _clockwise = true;
        func();
    }
    _lastState = _currentState;
}

    // Returns direction most recently turned, CW = true, CCW = false
bool Rotary::getClockwise(void){
    return _clockwise;
}

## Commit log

2024-03-05 Initial Commit, LCD Radar using ultrasonic sensor, distance sensing bit
2024-03-06 removed ultrasonic sens, update to mbed6, started my own lib for IR sens
2024-03-06 create pseudo3D image from depth data, (maybe this will be a 3d camera?)
2024-03-11 Created Servo Library, potentiometer now scales range
2024-03-11 Updated servo lib to work with custom servo parameters
2024-03-12 created stepper lib, fixed servo lib
    [main.cpp, myServo.cpp, myStepper.cpp]
2024-03-12 added half-step to stepper library
2024-03-13 added microstepping to stepper lib
2024-03-13 Fix silly mistake in drawRadarView angle offset, 315 - 90 = 225 (!255)
    [main.cpp]
2024-03-14 added rotary encoder library
2024-03-15 started using flags; also ERROR: rotaryencoder causes mutex in ISR
    [main.cpp, rotaryEncoder.cpp]
2024-03-16 started 3d lib, FIXME: rotary encoder calls button function when turned?
    [main.cpp, rotaryEncoder.cpp]
2024-03-18 added projection calculations to 3dlib, TODO: move camera
2024-03-18 Renders and rotates 3d cube, FIXME: rotate too far shrinks to infinity
    [main.cpp]
2024-03-18 50Hz rotating cube demo
2024-03-20 Comments+Formatting. Boots to 3d cube demo at 50Hz
2024-03-20 changed rotary encoder implementation to solve debounce issue
    [main.cpp, rotaryEncoder.cpp]
2024-03-25 Made button lib. Add Functionality: rotate around all 3 axis' via touch
2024-03-26 Cleaned button gui & optimized drawing. Added Feature: Focal-length/FOV
2024-03-26 Added Slidey Buttons
2024-03-26 Added button support for multiple simultaneous touches
2024-03-27 Removed "Magic Numbers". Updated vars with stricter (tighter) data types
    [main.cpp]
2024-03-27 Bugfixes: Vertices & Menu Index exceeding maximum. ScanAngle underflow.
    [main.cpp]
2024-03-31 Added dedicated thread to handle touchscreen button presses
2024-03-31 added mutex lock to TS button thread
2024-03-31 Fixed TS Button thread implementation, Added semaphore
    [main.cpp]
2024-04-01 Started adding Uart interface
2024-04-01 Streamlined Uart Implementation, Fixed semaphores
    [main.cpp, uartCommands.cpp]
2024-04-01 Fixed Flickering by waiting for V-Sync
    [main.cpp]
2024-04-01 reverted double buffering unless rotating model (too many issues)
    [main.cpp]
2024-04-01 Implemented Uart Command to start scan
2024-04-01 fixed encoder menu not clearing screen
    [main.cpp]
2024-04-01 Uploaded 3D printed mount STL
    V4 of the mount I made to house the servo & IR sensor, and attatch them to the stepper.
    [Angelo_IR_Mount_V4.stl]
2024-04-01 Created Folder for 3D print files
2024-04-01 Uploaded Mount V4
    [Angelo_IR_Mount_V4.stl]
2024-04-01 Added images to readme, corrected spelling
    I cant spell without autocorrect apparently, added images of 3D Printed mount
2024-04-02 Fixed servo timing
